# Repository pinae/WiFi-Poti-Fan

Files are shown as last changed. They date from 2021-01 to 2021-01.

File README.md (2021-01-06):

# WiFi-Poti-Fan
Fan controller with a WiFi controlled ESP8266.

This circuit controls 4 pin fans which accept a 25kHz PWM signal for speed control. It was tested with 5V and 12V fans - please select the step down converter accordingly. The ESP12F always runs with 3,3V so even the 5V version needs a voltage regulator.

| #  | **Components** |
|----|---|
| 1x | ESP12F |
| 4x | 10kΩ resistor |
| 1x | 10μF elko |
| 1x | 100nF ceramic capacitor |
| 2x | push button |
| 1x | trim potentiometer |
| 1x | linear potentiometer |
| 1x | 6 pin pcb connector |
| 1x | 5mm drum socket |
| 1x | 12V or 5V step down converter  |
| ?  | as many 4 pin fans as you like |

Additionally you need an FTDI adapter for programming.

You also need a power supply which depends on the fans you are using. One 5V fan can easily be supplied with a USB cable connected to a notebook. 25 12V fans work well with a power supply with 2 A.

## Circuit

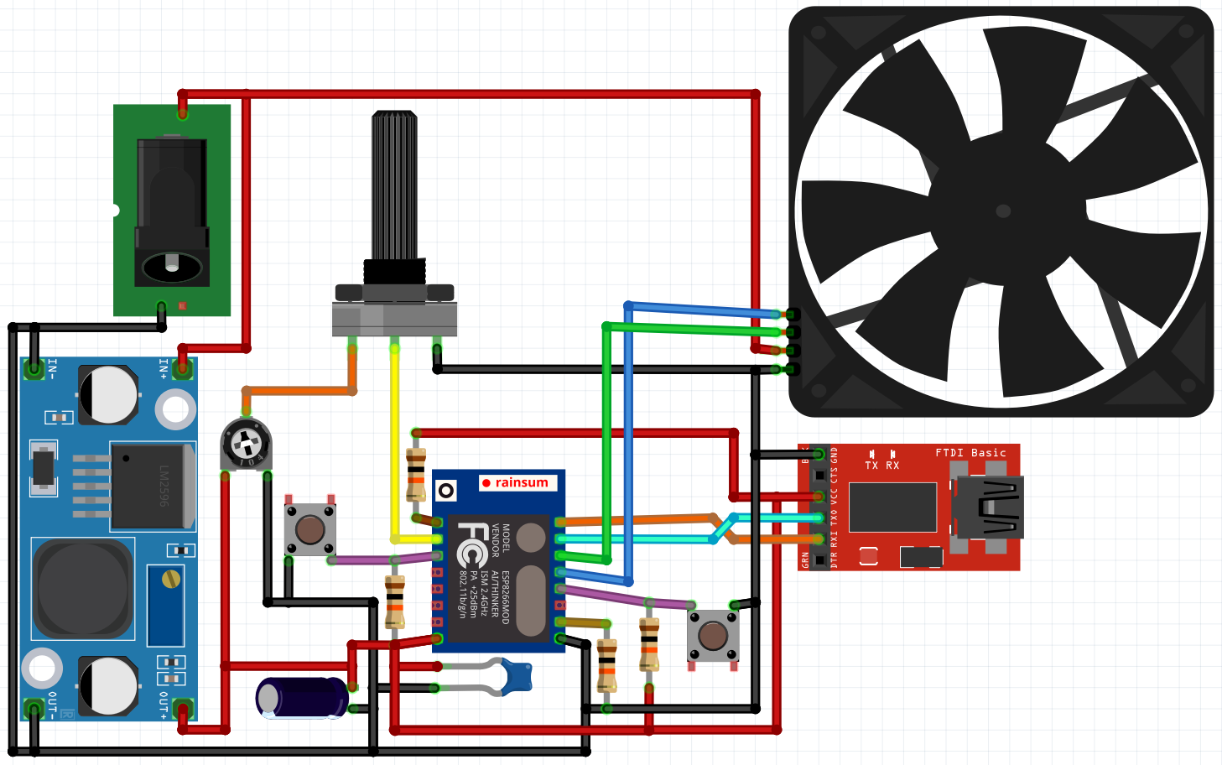
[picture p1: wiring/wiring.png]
The fritzing diagram shows how to connect the components


There is a schematic exported from fritzing [here](wiring/Schaltplan.pdf). You may modify the [fritzing file](wiring/Schaltplan_Luefter.fzz) if you like.

If you want to connect more than one fan just supply the pwm signal to all of them. This works fine if you trust in the capability of the fans to control themselves. Leave the connection for the tache signal connected to the first fan. You may use free pins on the ESP to connect additional tachs signals but the pin count of the ESP is very limited. With 25 fans you just have to believe in their capability to control themselves and skip the feedback.

## Programming

This software is designed to be flashed with [PlatformIO](https://platformio.org/install/ide?install=vscode). All the dependencies are noted in [platformio.ini](platformio.ini).

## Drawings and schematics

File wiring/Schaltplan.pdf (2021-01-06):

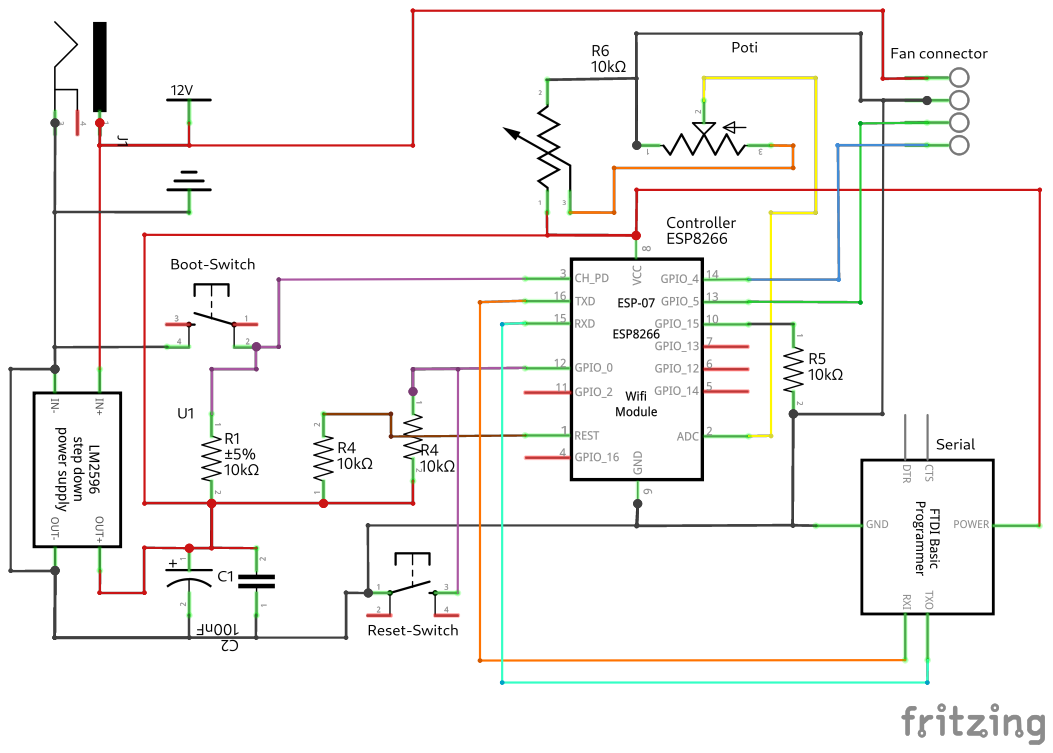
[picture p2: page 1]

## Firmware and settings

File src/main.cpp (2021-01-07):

#include <Arduino.h>
#include <ESP8266WiFi.h>
#include <IotWebConf.h>
#include "debugLogger.h"
#include "mqtt.h"
#include "configHelpers.h"
#include "conversionHelpers.h"

#define TACHO_PIN 5
#define FAN_PWM_PIN 4
#define CONFIG_VERSION "v0.2.1"

DeviceName devName;
DebugLogger logger;
unsigned long lastTrigger;
int mode = MODE_MANUAL;
int setSpeed = 25;
int lastManualValue = 0;
unsigned long reportTimer = 0;
unsigned long lastSpeedReport = 0;
float fanSpeed = 0;
const char wifiInitialApPassword[] = "loving_ct";
DNSServer dnsServer;
WebServer server(80);
IotWebConf iotWebConf(devName.get(), &dnsServer, &server, wifiInitialApPassword, CONFIG_VERSION);

ICACHE_RAM_ATTR void onFanRotation() {
  unsigned long now = millis();
  //logger.printf("onFanRotation: %ul %ul\n", lastTrigger, now);
  reportTimer += now-lastTrigger;
  if (reportTimer > 5000) {
    reportTimer = 0;
    fanSpeed = 60000/(now-lastTrigger);
  }
  lastTrigger = now;
}

float voltageToAngle(float voltage) {
  return 3.16306348e-86 * pow(voltage - 4.62751482e+02, 33) + 5.33460164e-03 * voltage + 1.81394601e+02;
}

void setup() {
  Serial.begin(115200);
  pinMode(LED_BUILTIN, OUTPUT);
  digitalWrite(LED_BUILTIN, LOW);
  pinMode(TACHO_PIN, INPUT_PULLUP);
  pinMode(FAN_PWM_PIN, OUTPUT);
  analogWriteRange(PWMRANGE);
  analogWriteFreq(25000);
  lastTrigger = millis();
  attachInterrupt(digitalPinToInterrupt(TACHO_PIN), onFanRotation, RISING);
  analogWrite(FAN_PWM_PIN, constrain(map(setSpeed, 0, 100, 0, PWMRANGE), 0, PWMRANGE));
  while(!Serial) {}  // Wait for Serial to start
  initWifiAP();
  reportTimer = 0;
  devName.print();
  Serial.println("\n\nSetup complete.");
  digitalWrite(LED_BUILTIN, LOW);
}

void loop() {
  //Serial.println("Loop iteration.");
  unsigned long now = millis();
  logger.printAllWithSerial();
  iotWebConf.doLoop();
  loopWifiChecks();
  int a = analogRead(A0);
  if (mode == MODE_MANUAL) {
    lastManualValue = constrain(map(a, 5, 1022, 0, PWMRANGE), 0, PWMRANGE);
  }
  if (mode == MODE_SET) {
    int newManualValue = constrain(map(a, 5, 1022, 0, PWMRANGE), 0, PWMRANGE);
    //Serial.printf("Checking if abs(%d - %d)=%d is more than %f.\n", 
    //  newManualValue, lastManualValue, abs(newManualValue - lastManualValue), PWMRANGE/3.0);
    if (abs(newManualValue - lastManualValue) > PWMRANGE/3.0) {
      mode = MODE_MANUAL;
      lastManualValue = newManualValue;
      Serial.printf("Switched to manual at %f%%.\n", ((float) newManualValue)/PWMRANGE*100.0);
    }
  }
  //Serial.printf("%d Manual value: %d\n", mode, lastManualValue);
  switch (mode) {
    case MODE_SET:
      analogWrite(FAN_PWM_PIN, constrain(map(setSpeed, 0, 100, 0, PWMRANGE), 0, PWMRANGE));
      break;
    case MODE_MANUAL:
      analogWrite(FAN_PWM_PIN, lastManualValue);
      break;
  }
  if ((now-lastSpeedReport) > 5000) {
    char* fanSpeedStr = (char*) malloc(50);
    sprintf(fanSpeedStr, "%.1f", fanSpeed);
    publishToMqtt("currentFanSpeed", fanSpeedStr);
    Serial.printf("Fan speed: %s rpm.\n", fanSpeedStr);
    free(fanSpeedStr);
    lastSpeedReport = now;
  }
}

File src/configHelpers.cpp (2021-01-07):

#include <Arduino.h>
#include <ESP8266WiFi.h>
#include <IotWebConf.h>
#include "debugLogger.h"
#include "conversionHelpers.h"
#include "configHelpers.h"
#include "webHandlers.h"
#include "mqtt.h"

#ifndef CONFIG_GLOBALS
#define CONFIG_GLOBALS
#define STRING_LEN 128

char mqttServerValue[STRING_LEN];
char mqttPortValue[6] = {'1', '8', '8', '3', '\0', '\0'};
char mqttUserNameValue[STRING_LEN];
char mqttUserPasswordValue[STRING_LEN];
extern WebServer server;
HTTPUpdateServer httpUpdater;
extern IotWebConf iotWebConf;
IotWebConfParameter mqttServerParam = IotWebConfParameter(
    "MQTT server", "mqttServer", mqttServerValue, STRING_LEN);
IotWebConfParameter mqttPortParam = IotWebConfParameter(
    "MQTT port", "mqttPort", mqttPortValue, 6, "text", "1883", "1883");
IotWebConfParameter mqttUserNameParam = IotWebConfParameter(
    "MQTT user", "mqttUser", mqttUserNameValue, STRING_LEN);
IotWebConfParameter mqttUserPasswordParam = IotWebConfParameter(
    "MQTT password", "mqttPass", mqttUserPasswordValue, STRING_LEN, "password");
bool needReset = false;
bool wifiIsConnected = false;
extern int mode;
extern int setSpeed;
extern int lastManualValue;
extern DebugLogger logger;

#endif

DeviceName::DeviceName() {
    byte mac[6]; WiFi.macAddress(mac);
    char macStr[18];
    sprintf(&macStr[0], "%x:%x:%x:%x:%x:%x", mac[0], mac[1], mac[2], mac[3], mac[4], mac[5]);
    strncpy(&deviceNameStr[14], macStr, 18);
}

void DeviceName::print() {
    byte mac[6]; WiFi.macAddress(mac);
    char macStr[18];
    sprintf(&macStr[0], "%x:%x:%x:%x:%x:%x", mac[0], mac[1], mac[2], mac[3], mac[4], mac[5]);
    logger.printf("MAC:\t\t%s\n", macStr);
    logger.printf("Device Name:\t%s\n", deviceNameStr);
}

char* DeviceName::get() {
    return &deviceNameStr[0];
}

void wifiConnected() {
    wifiIsConnected = true;
}

void configSaved() {
    //Serial.println("Configuration was updated.");
    needReset = true;
}

void initWifiAP() {
    //Serial.println("Initializing WiFi...");
    iotWebConf.addParameter(&mqttServerParam);
    iotWebConf.addParameter(&mqttPortParam);
    iotWebConf.addParameter(&mqttUserNameParam);
    iotWebConf.addParameter(&mqttUserPasswordParam);
    iotWebConf.setConfigSavedCallback(&configSaved);
    iotWebConf.setWifiConnectionCallback(&wifiConnected);
    iotWebConf.setupUpdateServer(&httpUpdater);
    boolean validConfig = iotWebConf.init();
    if (!validConfig) {
        mqttServerValue[0] = '\0';
        mqttUserNameValue[0] = '\0';
        mqttUserPasswordValue[0] = '\0';
    }
    server.on("/", handleRoot);
    server.on("/config", []{ iotWebConf.handleConfig(); });
    server.onNotFound([](){ iotWebConf.handleNotFound(); });
}

char* getMqttServer() {
    return mqttServerValue;
}

unsigned long getMqttPort() {
    int portVal = strToInt(mqttPortValue);
    if (portVal < 0) return 1883;
    return portVal;
}

char* getMqttUsername() {
    return mqttUserNameValue;
}

char* getMqttPassword() {
    return mqttUserPasswordValue;
}

void setFanSpeed(char* payload) {
  int speedInPercent = strToInt(payload);
  if(speedInPercent >= 0) {
    logger.printf("MQTT Message: Switching to set mode.\nSetting fan speed to %d%%.\n", speedInPercent);
    setSpeed = speedInPercent;
    mode = MODE_SET;
    int a = analogRead(A0);
    lastManualValue = constrain(map(a, 5, 1022, 0, PWMRANGE), 0, PWMRANGE);
  } else {
    logger.printf("The over MQTT requested speed (%s) was not a number in percent.\n", payload);
  }
}

void mqttSubscribe() {
  subscribeToTopic("setFanSpeed", setFanSpeed);
}

void loopWifiChecks() {
    mqttSetup(mqttSubscribe);
    mqttLoop();
    if (needReset) {
        Serial.println("Rebooting after 1 second.");
        iotWebConf.delay(1000);
        ESP.restart();
    }
}

void iotWebConfDelay(unsigned long duration) {
    iotWebConf.delay(duration);
}

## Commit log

2020-08-13 Firmware is working (poti, no WiFi)
    [angles-values.ods]
2020-09-01 Reporting rpm via MQTT and switching modes if requested.
2020-09-01 Reset wifi manager if EEPROM settings are missing
    [main.cpp]
2020-09-17 start the fan slowly if no wifi is configured
2020-12-19 changed wiring for linear poti and switched to IotWebConf
2021-01-06 added fritzing data
    [Schaltplan_Luefter.fzz]
2021-01-06 Corrected middle connection of the poti
    [Schaltplan_Luefter.fzz]
